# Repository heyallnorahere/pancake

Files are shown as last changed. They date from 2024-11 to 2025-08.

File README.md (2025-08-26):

# pancake

Pancake bot.

CAD drawing can be found [here](https://cad.onshape.com/documents/24af23b84924bcae2e494b27/w/7822e903a0ddc4106c8a2e95/e/12f5b05b2e40a2d157e12141).

Robot
*final robot*

## What is this?

This is a robot based on a "swerve" drivetrain as seen in FIRST Robotics Competition (FRC). The goal
of the project is to build a robot from the ground up, with the only caveat being that off-the-shelf
FRC parts are used exclusively for motors and electrical systems.

A characteristic of the swerve drivetrain is that the robot can move in a linear direction and
rotate at the same time. This is achieved through independent motion of all "modules" - a "module"
controls the motion of one wheel. Each module has the capability to both orient its wheel
independently all of the other wheels and also drive the wheel at the same time. This works with the
use of 2 motors per wheel - one which drives the speed of the wheel, and one which controls the
angle at which the wheel applies force. As a result of this design, my robot is able to move in a
linear direction and rotate concurrently.

Instead of using a roboRIO as robots in FRC do, this project uses a Raspberry Pi. I chose this in
order to build my own tech stack, instead of depending on the robot control systems that are
pre-built for FRC. I also used a single-board computer such as this in order to use low-level APIs
such as CAN without relying on vendor libraries to control motors and such.

This robot is not FRC-legal. The main component which disqualifies it is the custom tech stack which
I wrote on top of ROS and the Raspberry Pi.

## But why?

I started this project to create a deeper understanding of the process of designing and building a
robot. When starting on my local FRC robotics team, I was confined to the bubble of the programming
sub-group. I used this project to break out of that bubble and engage in more aspects of the
process, such as CAD, electrical systems, mechanical assembly, and the interface between user-space
robot code and electrical I/O.

I chose the object of just recreating a swerve drivetrain because it was a complex idea that would
produce a cool result. I had an intuition for how it worked when I was just working on the team, but
I wanted to find out for myself how easily it was implemented and what concessions had to be made
for practicality.

## How?
### Spinning a motor
#### CAN interface

In FRC, CAN is the primary protocol with which the roboRIO interfaces with motors. The Raspberry Pi
does not come with a native CAN interface, in contrast to the roboRIO's built-in CAN ports. With
this being said, however, commercial auxiliary CAN hats can extend the Raspberry Pi's hardware
functionality through the use of the Raspberry Pi's
[SPI](https://en.wikipedia.org/wiki/Serial_Peripheral_Interface) interface, and provide a CAN
network exposed to user-space Linux programs, such as my robot code.

#### SOLO

I chose a Raspberry Pi to control the robot for several reasons. It's cheap, supports a widely-used
operating system, runs on very little power (<1 amp @ 5V), and it does not require an SDK or
specialized development environment to develop for it. While researching the requirements for this
project, however, it was very difficult to find any motor controllers that fell within the budget of
this project while also being guaranteed to work on any CAN-supported computer.

The best candidate I could find that fit both of these criteria was
[SOLO Motor Controllers](https://solomotorcontrollers.com), based out of Europe. Specifically, their
UNO v2 controller with its 45A max current. The only issue was that one controller costed 239 euros
(around 278 USD). Despite the cost, however, this was still the cheapest option that was not
confined to a proprietary ecosystem. I ordered 2 controllers for testing and development purposes so
that I could design and build a module while waiting for more to arrive.

SOLO controllers communicate with their controlling devices via CANopen, among other supported
protocols. I decided to stick with a CAN protocol due to its proliferation in FRC. SOLO provides
a library in both Python and C++ to communicate with their controllers. I was drawn to using their
C++ API due to my familiarity with native programming. However, the C++ library was written locked
to Windows, and my device of choice was running a distribution of Linux. It's not very feasible to
install Windows on a Raspberry Pi, nor was embedding Windows an attractive option from a familiarity
perspective. I had an Intel Nuc that I had installed Windows on, however it was not common to attach
a CAN interface to a computer through USB, and I was also just averse to Windows. I had already
bought a CAN hat for the Raspberry Pi, so the Python API seemed like my best option, as
uncomfortable as I was with the language.

#### NEO Vortex & NEO 550 motors

The most common type motor in FRC is **brushless DC** (BLDC). These motors generally have high
torque and top speed. Initially, I planned to drive both the wheel's speed and orientation using the
same kind of motor, the [NEO Vortex](https://revrobotics.com/rev-21-1652) from REV Robotics. I chose
this motor because it has a relatively high stall torque, and it is widely used in FRC.

This motor is designed to work with either a [SPARK Flex](https://revrobotics.com/rev-11-2159)
controller or a [Solo Adapter](https://revrobotics.com/rev-11-2828) together with a
[SPARK MAX](https://revrobotics.com/rev-11-2158) controller. Due to my previous initial decision of
using a SOLO controller, I decided to buy 2 of both Vortex motors and Solo Adapters. Before I did
this, however, I emailed REV Robotics to verify that a Solo Adapter would work with a generic BLDC
motor controller, to which they affirmed yes. With their confirmation, I ordered the motors and
adapters.

When the Vortex motors and SOLO controllers arrived, I decided to wire one set up for testing.
I assembled the motor onto the Solo Adapter, connected the three phase wires to the SOLO controller,
and powered the SOLO controller with an oscilloscope power supply. However, I also needed to connect
the internal encoder to the controller. The encoder allows the computer to receive feedback from the
motor about how fast it's moving, and how much it's moved since it was powered on. I cut the 6-pin
JST encoder cable that came with the Solo Adapter to half length, and soldered it to the
smaller-pitch 6-pin JST cable, using mappings for the cable found on
[REV's docs](https://docs.revrobotics.com/brushless/spark-max/specs/encoder-port) and the UNO v2
[user manual](https://solomotorcontrollers.com/wp-content/uploads/materials/SOLO_UNO_v2_SLU0722_5832_UserManual.pdf).
This allowed me to spin the motor through the controller's UART interface.

When I began designing the module, I realized that for module azimuth, I did not need
nearly as much torque AND speed as the Vortex provided. In order to minimize both power usage and
project cost, I replaced the azimuth motor with a [NEO 550](https://revrobotics.com/rev-21-1651)
motor in my design, and ordered one motor. I also connected the motor to a set of gearboxes which
decreased its gear ratio by 1:12, increasing its torque while decreasing the speed at which the
wheel rotates in relation to the motor's speed. This can be easily accounted for in code.

#### SPARK MAX

As I was noticing the corner of unfamiliarity I was backing myself into with my developing tech
stack, I decided to send an email to REV Robotics concerning the API for their proprietary motor
controller, the SPARK MAX. I was familiar with this controller due to my experience programming on
an FRC team. This seemed like an amazing alternative to SOLO due to its much cheaper cost of 90 USD.
I asked if there was a library for desktop development environments that I had missed for
communicating with their motor controllers, or if they could provide me with the CAN protocol details
if they did not have such a library published. To my surprise, they sent me a spreadsheet describing
the details of SPARK MAX CAN frames. This gave me a viable alternative to the much more expensive
SOLO controllers.

After careful consideration, I decided to substitute the SOLO controllers for SPARK MAXs. I scrapped
the Python code that I had written to communicate with the controllers, and I ordered 1 SPARK MAX,
learning from my mistake previously of ordering 2 controllers to test. It was also convenient that
the controllers shipped from the US, rather than Italy.

As I now had to write my own API for CAN communication, I was able to write my new stack in a
language I was more familiar with. With Python off the table, I was opting towards C++. I briefly
considered Java, being both the most common language in FRC and also the language that my team works
in. However, I would need to waste time working with the Java Native Interface, communicating
directly with the Linux kernel. This seemed like too much of a hassle in a language that was both
abstracted from low-level APIs and not my language of choice, so I decided to stick with my comfort
language: C++.

CAN on Linux works by opening a socket on the `canX` network, with `X` being the interface index.
This allows one to send CAN frames on the electrical CAN network via the ubiquitous Linux socket
API. Through Googling I came across this great
[document](https://kernel.org/doc/Documentation/networking/can.txt) which describes how the socket
CAN interface is used. This greatly sped up the software development process.

There are many protocols through which functionality is exposed over CAN. The most common one by far
is CANopen, which is used in industry robotics and medical equipment. FRC, however, has
[their own CAN protocol](https://docs.wpilib.org/en/stable/docs/software/can-devices/can-addressing.html).
Even so, this specification does not explain on its own how to communicate with one specific kind of
motor controller. This in combination with the spreadsheet that REV support shared with me made it
possible for me to begin working on my own library to communicate with SPARK MAX controllers.

After much writing, debugging, and emailing, I was able to write my own vendor library to control
DC/BLDC motors through SPARK MAX controllers. However, REV stipulated that I cannot share the
details of the CAN spec, so the `vendor/librevfree` submodule (the library that I wrote to interface
with the motor controllers) is not made public.

I had issues with motor controllers later down the road. Accordingly, I continued to commit to the
library as I was developing the robot. It's very hard to write your own library and use it without
finding issues.

### Software development

FRC relies upon a proprietary control system integrated with an NI roboRIO. It sends signals through
the control client to dictate which WPILib routines run on the roboRIO ("Teleop" or "Autonomous")
during various phases of each FRC match. It also handles controller input during the teleoperated
mode to allow the user to control the robot directly.

As I was operating in my own development environment, I had none of these luxuries. I had to choose
how exactly I wanted to design my robot system.

#### Communication via ROS & Docker

Because this project uses a Raspberry Pi, I needed some way to communicate with a control system. I
used ROS (**R**obot **O**perating **S**ystem) to achieve this. ROS is a tech stack designed for
interoperation between multiple processes running either on the same computer or multiple in a
closed system. It natively supports C, C++, and Python, which fit any conceivable use case I had for
it in this project. 

An ROS application consists of a system of "nodes," individual processes on various devices which
send arbitrary messages to each other. The ROS message system is identical to FRC's
publisher/subscriber system, where server nodes send messages on "paths" akin to Unix file paths for
client nodes to listen to.

ROS is not natively supported on any Linux distributions other than Ubuntu. The Raspberry Pi only
directly supports its own version of Debian called Raspberry Pi OS, or Raspbian. Although Ubuntu is
closely related to Debian through its package manager and source tree, the two distributions use
different package repositories, and for the robot's runtime environment, I wanted the package
manager system to be as clean as possible, without any hacked-together package manager
configuration.

I considered installing Ubuntu on the Raspberry Pi that I mounted onto the robot, however Docker
seemed like a much better choice. Docker is a background process that runs containerized versions of
operating systems pre-installed with a desired program. It's useful for "shipping" the *exact*
runtime environment that you want your program to run in. With Docker, I could control explicitly
for the runtime environment of my project using my custom-built Docker image.

Docker also allows the image to have controlled access to the host computer's peripheral devices.
This includes the CAN network and game controllers. Passing through the host networks and input
devices, I was able to precisely control the methods in which my program could interact with its
host environment. This is very useful for creating security sandboxes, minimizing the chance that a
vulnerability in my tech stack could compromise my workflow and the end product.

Deciding to ship my software stack with Docker, I set up a Docker build in my code tree. As I was
hosting my project's code using a private Github repository, I had limited monthly access to Github
Actions, their CI/CD system, a service which runs automated tasks when it receives events. My access
was limited by job run time, however my builds were infrequent enough that I was able to build the
Docker image for both x86 and ARM architectures every time that I pushed a commit. As I used CI/CD
more frequently, and I wanted to control the hardware that it was built on, I began using a desktop
computer installed with an Ubuntu server to act as an Actions runner for my project, lifting the
usage restrictions.

#### Cross-compilation

Single-board computers such as the Raspberry Pi run on the ARM CPU architecture. This differs from
the x86 architecture that most desktop, laptop, and data center machines run on. However, because I
was developing the project in C++, and the native Linux ELF binaries that C and C++ compile to
cannot run on architectures they were not compiled for, so I was forced to compile my ROS project
explicitly for `arm64`. Initially, I emulated the `arm64` architecture during the Docker build via
QEMU in my CI/CD workflow. However, each build took around 30 minutes due to the compiler overhead
introduced with C++ templating, and the proliferation of templates in the ROS C++ client library.

The more efficient approach I devised was to segment the Docker build into two stages: `build` and
`runtime`. The `build` stage runs on the native architecture of the compilation machine, while the
`runtime` stage runs on the target architecture that the image will be built for. The project is
cross compiled in the `build` stage using compiler wizardry and
[shell scripts](scripts/buildenv.sh). After this, the binaries are copied into the `runtime` stage,
and the robot code can run natively on the Raspberry Pi through the Docker hypervisor.

#### Robot input & SDL

FRC uses conventional game controllers to control competition robots. The most common controllers
used are those of the Xbox 360, Xbox One, and PS4. These controllers are all supported by
[SDL](https://github.com/libsdl-org/SDL), a library for GUI applications with real-time input,
designed for applications such as game development. As I was already familiar with the library's
usage, I decided to use this library to handle controller input on the robot. It can be built
headless (without windowing support) using a configuration flag (`-DSDL_VIDEO=OFF`) so that it
builds in less time without unnecessary features.

I used SDL in an independent `client` ROS node to handle controller input from the user, and pass
messages along to the `robot` node. I also wrote a simple GUI client in the same `client` node using
[Dear ImGui](https://github.com/ocornut/imgui) in case the library was built with video support,
i.e. in desktop environments for simulation and remote control.

#### Drivetrain control

The main meat and potatoes of my application is in the `swerve` ROS node. Receiving messages from
its controlling `robot` node, it derives motor voltages from the `robot` node's "request" using
geometric, trigonometric, and physical principles. It then sends CAN messages to the SPARK MAX motor
controllers, which use their respective motor to produce torque on that motor's axis.

After it sends signals to its motors, it then uses the feedback of velocities reported by
aforementioned motors' encoders to determine the current velocity of each module. The data collected
on each module is then used to determine the linear and angular velocity of the entire robot in
order to inform how it continues to control each module. All of this data is published back to the
ROS message system for the `robot` and `client` nodes to use.

#### Self-updating & bluetooth controller pairing

I wanted this project to have the capability to run without any external computers or monitors. For
this purpose, I wanted to expose two helpful functions on the actual chassis of the robot:
self-updating and controller connection.

Due to the containerized nature of this project through Docker, new versions are easily installed by
downloading a new image and recreating the container using the newly-downloaded image. Because of
the simplicity of this process, a project called
[Watchtower](https://github.com/containrrr/watchtower) exists to automate it. With an option, it
exposes an HTTP REST API which allows clients to send HTTP requests to trigger container updates.

I wrote another containerized [program](https://github.com/heyallnorahere/robot-util) to expose this
functionality through a text UI on a small $10 20x4 HD44780 I2C LCD screen. It handles automated
image updates through a menu option which is selectable through a rotary encoder connected to the
Raspberry Pi's GPIO pins. I wrote this program in C both to stretch myself with a minimalist
programming language and because the program itself was not inherently object-oriented as the swerve
drivetrain was. It's containerized with Docker similarly to the actual robot code, and self-updates
through the same mechanism through which it updates the robot code.

I also created menu functionality to pair bluetooth devices. This is useful for pairing console
controllers, as oftentimes these controllers connect to their respective console through bluetooth.
This allows one to pair a controller to control the robot through the LCD screen, instead of having
to `ssh` into the Raspberry Pi and pair it manually through `bluetoothctl`.

### Chassis design

As the goal of this project was to gain experience with all aspects of robot design, I designed the
entire robot chassis from the ground up. In FRC, it is standard practice to buy manufactured swerve
modules from hardware vendors (i.e. REV, Swerve Drive Specialties), as the drivetrain is not the
primary hurdle of robot development. However, my focus was primarily on the intricate design process
of the *entire* robot, including the swerve modules. These were the first steps in robot
development.

#### CAD

Before this project, I had acquired some CAD (**c**omputer-**a**ided **d**esign) experience. In the
past, I had designed some robotics-adjacent projects with CAD software, however these projects never
came to fruition. This project seemed like a perfect opportunity to brush up on my CAD skills.

The software suite that I chose for this project was Onshape. Onshape is very commonly used in FRC
design teams, and I had used it in the past with physically-designed projects. It's also very
feature-complete with an extensible API for creating additional features.

#### Materials

The vast majority of mechanical parts in FRC are manufactured out of aluminum. During development, I
did not have access to a CNC router, so I chose the next best option, which I had plenty of
experience with: 3D printing. 3D printers can manufacture parts with plastics of varying tensile
strengths, which gave me confidence in the approach.

For parts such as gears that experience large amounts of force over very little surface area, I
decided to print with ASA (**a**crylonitrile **s**tyrene **a**crylate) filament, a thermoplastic
commonly used in the manufacturing of mechanical parts. However, as I was prototyping with PLA
(**p**oly**l**actic **a**cid) infused with ABS (**a**crylonitrile **b**utadiene **s**tyrene), I
found that parts printed completely filled with plastic held up very well under simulation of the
stress that they would experience. Drawing from this discovery, I decided to manufacture all parts
used in the swerve modules and electronics mountings with this blend of PLA and ABS.

I assembled the modules to the rest of the components using custom-cut 20x20 aluminum extrusions.
These were preferable to long, segmented 3D printed parts because the alternative would not be
nearly as structurally stable, nor would it be time- or cost-effective in comparison to extrusions.

#### Structure

Due to the flexibility in which one can design parts for 3D printers, and the availability of
breakaway support material, designing the structure itself was trivial. Each module consists of two
main plates, supported between each other with 3cm-long printed standoffs. 3D-printed parts are
extremely strong under compression, which led me to use them as nothing more than spacers, held in
place by M3x50 bolts on the top and M3 nuts on the bottom.

As the large majority of the module's weight lies on the top plate, it's very important that it's
adequately supported. With some quick Googling, I determined that PLA plates should be supported
roughly every 5cm. I shortened this slightly to 4.2cm both for convenience in my design and to
create a margin for printing and assembly error.

#### Hardware

Wherever possible, I stuck with metric units and bolt sizes. I had quite a lot of M3 hardware lying
around, so I used M3 whenever I could. However, I had to make some exceptions. To secure the two
internal drive gears to their respective shafts, I used an M2 bolt threaded through a nut in a small
pocket on the internal circumference of the gear. M3 screws were too large. In my mount for the
Raspberry Pi, I had to use M2.5 bolts to fit through the RPi's mounting holes. Additionally, all
FRC-legal parts use #10-32 bolts. In addition to the irritation of using imperial units, I did not
have any #10-32 hardware in stock.

I mounted each individual part onto the aluminum extrusions which joined the chassis together with
drop-in M3 T-nuts. On the uncut extrusions which I already had in stock, the T-nuts dropped in
perfectly. However, when the custom-cut extrusions I ordered from Misumi arrived, the lips on the
new extrusions did not allow the T-nut to drop in. This created a slight inconvenience whenever I
added a new part to the chassis, as I had to remove the entire extrusion from the chassis and slide
the necessary quantity of T-nuts down the shaft.

#### Design details

For a reference of how swerve modules commonly work, I at the CAD drawing for
[REV's MAXSwerve module](https://revrobotics.com/rev-21-3005/). As a result, the module was loosely
based off of this design. I also used their wheels in my design.

The module uses two motors in coordination to orient and drive the wheel independently. The module
is also fitted with a duty cycle encoder to measure the distance from the module's "default"
position. This allows the motors to control the direction and magnitude of force which the module
is exerting on the robot's chassis while also sending feedback to the robot's controlling device.

The drive motor has a nearly inconsequential gear ratio because the motor produces a large amount of
torque on its own. However, I attached two gearboxes to the rotational motor to decrease its gear
ratio by 1:12. This is further decreased by its 1:4 relation to the output orientation of the wheel,
which leaves the axis with a gear ratio of 1:48 to maximize torque.

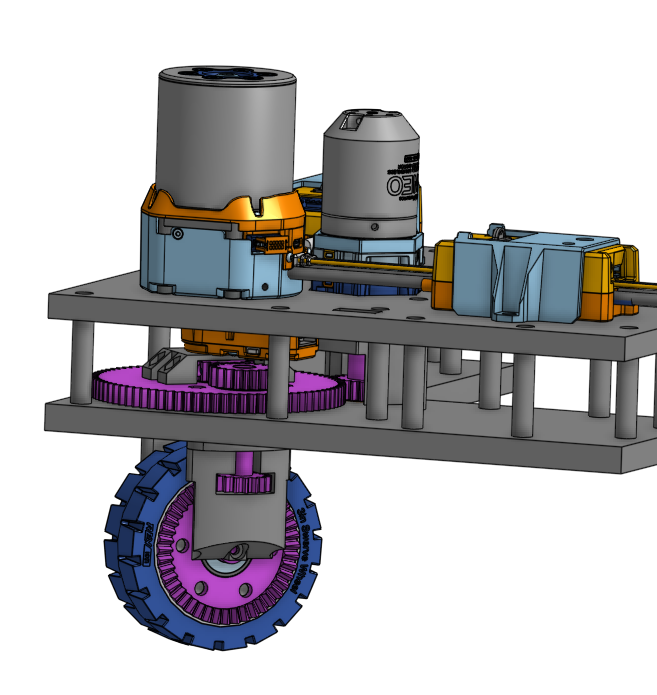
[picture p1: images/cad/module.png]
Module CAD

*CAD drawing of swerve module*

### Electronics

Robots need power. A lot of power.

#### Power delivery

FRC robots run on a nominal voltage of 12 volts. Typical SLA (**s**ealed **l**ead **a**cid)
batteries as used in FRC generally produce a voltage slightly higher, at 13 volts. To mimic the
final environment of an SLA battery, I ran motors on a 13V wall power supply while prototyping.
However, when I attached the modules to a full chassis, I began running the robot off of battery
power.

The battery is fed into a 120A breaker, common in FRC robots. This creates a hard upper limit for
the robot's power draw, mitigating the damage of short circuits and stalled motors. It also provides
a switch to turn the robot on and off immediately, a safer mechanism than simply attaching the
battery.

All power in the robot runs through a centralized device called a PDH (**P**ower **D**istribution
**H**ub), another FRC-standard component from the vendor of the motors and controllers I was using,
REV Robotics. It distributes power to multiple channels, each limited with a fuse or breaker. The
PDH was also ideal for testing and iteration, with WAGO clips on each channel for both VCC and
ground, as opposed to permanent crimping or soldering. The battery cables from the breaker run
directly into the PDH, where it distributes power and limits current draw from each motor.

I used 12AWG wire to connect the motor controllers to the PDH. 12AWG wire is rated for 20A
continuously, with a fusing current of over 200A. This was ideal for my application, as the maximum
current between both kinds of motor was 45A, and the force required to move the robot was not
particularly high. These wires were connected to the motor controllers with WAGO connectors,
similar to the PDH terminals.

#### Cable management

Due to the mobile nature of this project, I needed to organize cables very neatly to avoid snagging
on any variation in the surface on which it's driving. Wires snagging on external objects could
cause power loss and short circuits, which at 12 volts could potentially cause significant damage to
the robot and its environment.

To simply cable management, I used paired red and black 12AWG cable to deliver power to the motor
controllers. I also ran cables along the 20x20 extrusions of the chassis' frame to avoid a rat's
nest in the empty portions of the frame.

I initially considered zipties to fasten cables to the extrusions. However, these are very wasteful,
with any electrical change creating plastic waste in the form of the previous tie. Because of this,
I chose to use velcro cable ties, reusable organizational ties which fulfill the same purpose as
zipties.

## Overarching challenges

**Lack of documentation**. I initially chose SOLO controllers because SPARK MAX controllers,
although clearly the better alternative, did not have publicly available CAN documentation. Even
after emailing REV, and working with a spreadsheet of CAN IDs, I still struggled to piece together a
viable control library. I had to decompile the native roboRIO REV library with
[Ghidra](https://github.com/NationalSecurityAgency/ghidra) to find memory layouts for status frames
undocumented in REV's spreadsheet. Additionally, as the new FRC season started in January 2025, REV
released a new version of firmware which dramatically changed the CAN API. After struggling to find
any data related to this new firmware version, either through REV support or in decompiled C++ code,
I opted to use an older version of the controller firmware.

**Iteration times**. C++ code that includes ROS headers took significantly longer to build and
therefore iterate upon due to the prominent use of templating within the library. I mitigated build
times by optimizing the build process (i.e. building image on native architecture, minimizing header
inclusion in code), however each build of my robot code took around 10 minutes. Additionally, when
designing the robot in CAD, I made several mistakes in designing each part. Most parts in each
module on either the module's top or bottom plates, and so a part change often meant I had to
re-print one or both of the plates. Each plate took slightly less an hour to print, so at the worst,
one print to fix one part took upwards of 2 hours. This combined with reassembly time
dramatically slowed the build process.

**Module mounting**. The module was just slightly too thick between the top surface of the top
plate and the bottom surface of the bottom to mount onto aluminum extrusions on the bottom of the
module with M3x50 bolts. M3x60 bolts were slightly too long to create a strong connection between
the module and the robot frame, and M3x50 bolts had to be forced into the T-nuts on the bottom. To
solve this issue, I ordered non-standard M3x55 bolts, which cost significantly more than M3x50s or
M3x60s and took nearly a week to arrive after I realized the issue, however they were able to create
a strong mechanical connection when suspended above the bolt's counterbore slot with a washer.

**UltraPlanetary bolt snugness**. The azimuth motor's output is fed through two REV UltraPlanetary
gearboxes which decrease its gear ratio by 1:12. These gearboxes are fastened to the module and
motor using 6 M3x30 bolts fed straight through the gearboxes into the motor. The issue with this
design arises when the bolts are fastened too tightly, and the friction of the system increases
dramatically. However, when the bolts are not fastened tightly enough, the motor begins shifting as
torque is applied, damaging the motor over time. Additionally, the bolts loosen very easily. I
solved this issue by using locktite to lock the bolts in place relative to the motor, gearboxes,
and module.

**Module inversion**. As I was preparing to test the robot moving on the ground, I noticed that two
modules were spinning inverted from the direction they should have been spinning in. This bug took
me 4 days to fix, and was caused by three main things. I had confused the spaces in which the wheel
well was rotating. I had also normalized an angle incorrectly, leading to incorrect angle values
when performing math to determine in what direction each module should be spinning. Fixing these two
issues fixed one module's rotation, however one was still spinning in the wrong direction. This was
ultimately caused by the duty cycle encoder being calibrated in the opposite direction, which was a
simple human error. Fixing this final issue removed this roadblock.

**Ubuntu package versions and ROS cross-compilation environment**.
[ROS does not support native cross-compilation on the latest distribution.](https://github.com/ros-tooling/cross_compile)
Setting up a cross-compilation environment manually is black-magicky, installing multiple
architectures of the same development package onto the same "machine" (or in this case, image build
container). The Python development libraries a prime example of this, breaking each other when
package versions differ. Unfortunately, the ROS image has this installed by default for the build
architecture, and attempting to uninstall it in the container will uninstall the rest of ROS.
Additionally, the Python package in the x86 repository generally gets a version bump a day or two
before the `arm64` port repository. This makes cross-compilation impossible for the amount of time
the two versions differ, because the `arm64` version is not installable without the entire
uninstallation of ROS. Thankfully, this was only an issue once in the development process.

## What went well?

**Final product fit within original project parameters**. The overall design of the robot did not
differ from my original vision when starting the robot. Originally, I was going to use SOLO
controllers, but I switched to SPARK MAX controllers before mechanically designing the robot in CAD,
so no major reworks needed to be done.

**FRC skills**. As one of the main stated goals when starting this project, I made sure to design
the robot as similarly to an FRC bot as I could. This led me to design the robot from the ground-up
as somebody on the design team would; I connected and organized CAN, power, and encoder wires as one
on the "systems" team would do; and I assembled the robot from the ground up, gaining me experience
with the "mech" team process. I also had the opportunity to delve into the FRC-flavored CAN
protocol, which is a step up from my previous experience on the programming team.

**No major electrical mistakes**. Even though it takes a large voltage to send a dangerous current
through the human heart due to the resistance from the end of one arm to the other, short circuits
directly between battery leads are potentially very dangerous. For this reason, I kept all wires
under fuses when possible, and I kept the PDH unplugged from power while managing wires. Because of
this, I never had any major electrical incidents while working on the robot. The only mistake that I
made in this regard was a particularly unfortunate accident when I sent a static shock through the
CAN hat of the Raspberry Pi and fried the board with a short. The Raspberry Pi was not harmed at
all, however I had to replace the CAN hat which cost $60 and a week.

**Communication protocol**. ROS supplies a robust real-time communication framework for coordination
between ROS nodes. This allowed me to easily segment the codebase and handle user input
independently of drivetrain math and motor control, among other development niceties.

**Automated build process**. As a result of my cloud-based cross-compilation setup, I was able to
streamline my workflow to automatically build and deploy my code every time I push a Git commit.
This allowed me to push my code to the robot and check in my current code state in one command in
Neovim, my code editor of choice.

**Self-contained final robot**. Early on in the project, I made the decision to consolidate all
necessary functions into the robot itself. This includes connection and collection of user input,
and also code updates. I implemented the self-contained connection of controllers using the Linux
BlueZ bluetooth stack, and I passed all user input devices through to the Docker container driving
the robot to be handled by the headless `client` node. I also implemented self-updates using
`watchtower` in combination with my LCD text UI, thus allowing the user to completely control the
robot and its software without the use of a shell.

## Lessons learned
### TRIPLE CHECK

This goes for CAD, programming, electrical work, all of it. Triple check your work! Do not write or
do something once and call it good. In CAD, make sure that one change in a seemingly unrelated area
did not break a part somewhere else. In software, unit test areas of code individually and
iteratively before testing it on the robot. In electrical work, triple check that all wires are
connected to the right components. All of this will solve so many debugging headaches.

### DONT BE LAZY AND FIX PROBLEMS

I spent too much time twiddling my thumbs while waiting for my robot code to build in Github CI.

XKCD 303 (https://xkcd.com/303/)
*XKCD 303: Compiling*

Before I sped up the build process by 1. hosting the build on my own server and 2. cross-compiling
code rather than emulating the compiler with QEMU, I thought, "it can't be helped. I need to just
keep working while the build finishes." This ultimately exaggerated iteration times and slowed the
build process.

Finally, I invested time into fixing the build system. With the ~5 hours that it took to get this up
and running, I had more than made up for the >15 (5 * 60 / (30 - 10)) builds that I had triggered by
that point. With a 10 minute build time, I was able to iterate at a much faster pace, allowing me to
dramatically speed up the development process.

### FINALIZE CORE COMPONENTS BEFORE ORDERING

I wasted around slightly less than $600 on SOLO motor controllers. The only reason I found it
reasonable to spend this much on motor controllers is that they are one of the core components that
makes this project possible. What I should have done before ordering the SOLO controllers was
confirm, beyond a shadow of a doubt, that these controllers were the ones that I would use. Although
it was ultimately beneficial that I emailed REV, I should have done that in the first place before
deciding on a motor controller.

### NEW TECHNOLOGIES USED

In the process of creating the end product, I introduced myself to quite a few new technologies. To
name a few, I familiarized myself with CAN for motor communication, the Linux D-Bus for
communication with the `bluetoothd` daemon, and cross-architecture C and C++ compilers and build
tools for my cross-compilation Docker toolchain. I also gained a lot of practical experience with
CAD, which greatly helps any personal and team projects that I might participate in. It is almost
always beneficial to use new and unfamiliar technologies in non-commercial projects in an effort to
become more well-rounded as a software developer.

### STAY ON TASK

I spent a few days trying to read data from the PDH over CAN for motor power usage metrics. This did
not end up proving useful or necessary, nor was it part of the project parameters, and I ultimately
just wasted my time. I could have used this time to work further towards the material goal of
finishing the robot.

### SAFETY FIRST AND BEFORE EVERYTHING

The incident with frying the CAN hat easily could have been avoided if I followed electrical safety
procedures. This happened in May, and it was particularly dry around this time. As a result, I
easily accumulated static charge by performing basic tasks. In addition to this, I was wearing a
cashmere hoodie, and my long hair was not tied back. When I went to rearrange CAN wires, I did not
ground myself before doing so. I accidentally delivered a static shock which stuck the board in a
configuration state.

I could have avoided this if I took my hoodie off, tied my hair back, and grounded myself before
working with delicate electrical equipment such as this. Safety procedures exist for a reason.

### DEBUGGING IS BETTER THAN NOTHING

While I was debugging the issue of inverted wheel rotation, I was confident that the issue was
ultimately in my swerve math. While this was somewhat correct, I was stuck looking over my math code
for around a day. Finally, I swallowed my pride and brought up a Docker container with `gdb` set up.
I had initially avoided this because I had only debugged code in an IDE's UI before. Additionally,
because the Docker build was segmented and the runtime stage did not have the source included in the
container tree, I had to cross-reference debugger output with my current source tree in Neovim.
Nonetheless, using a debugger greatly sped up my debugging process, and it likely allowed me to
solve the issue much quicker than if I had not brought up a debugger. I learned that I need to
broaden my approach to solving problems, consider new approaches that I had not tried yet, and check
null hypotheses.

## What's next?

The main feature I would like to implement is autonomous motion on pre-programmed paths, based on
computer vision. I have experience with this in FRC, using libraries such as
[PhotonVision](https://github.com/PhotonVision/photonvision) for computer vision, and
[PathPlanner](https://github.com/mjansen4857/pathplanner) for path generation. These libraries are
built specifically for FRC, so plug-and-play use in my project is likely unfeasible. Implementing
motion along paths seems to be easily achievable with my experience with the library. Additionally,
the University of Michigan provides a native, open-source
[library for detecting April Tags](https://github.com/AprilRobotics/apriltag), the specification of
fiducial tags used in FRC. With both of these components, this feature seems completely feasible.

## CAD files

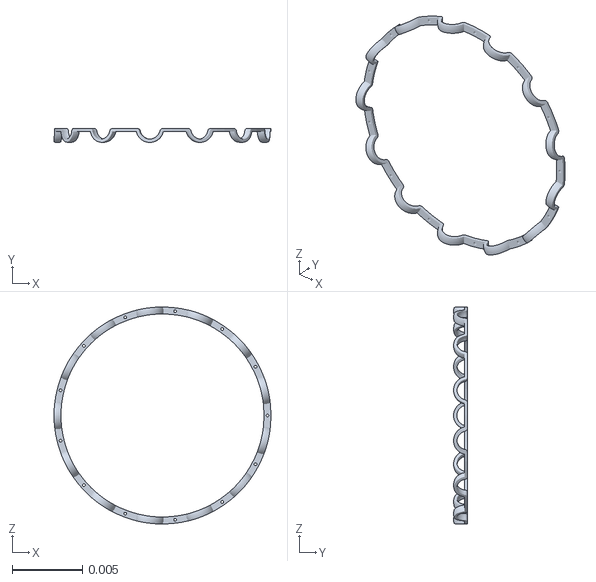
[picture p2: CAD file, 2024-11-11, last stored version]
resource/cage.stl
0.0155 x 0.000994 x 0.0155

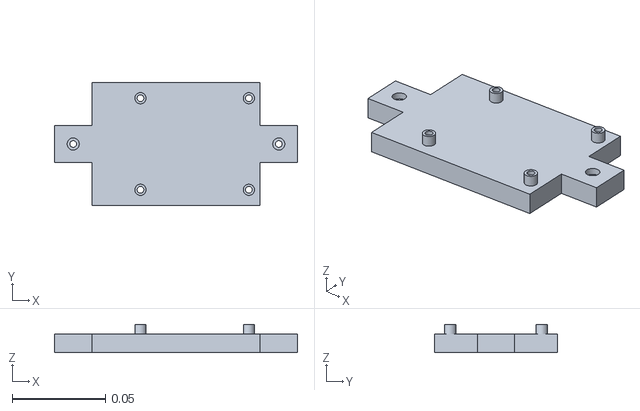
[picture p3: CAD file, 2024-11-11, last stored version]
resource/rpi_plate.stl
0.13 x 0.066 x 0.015

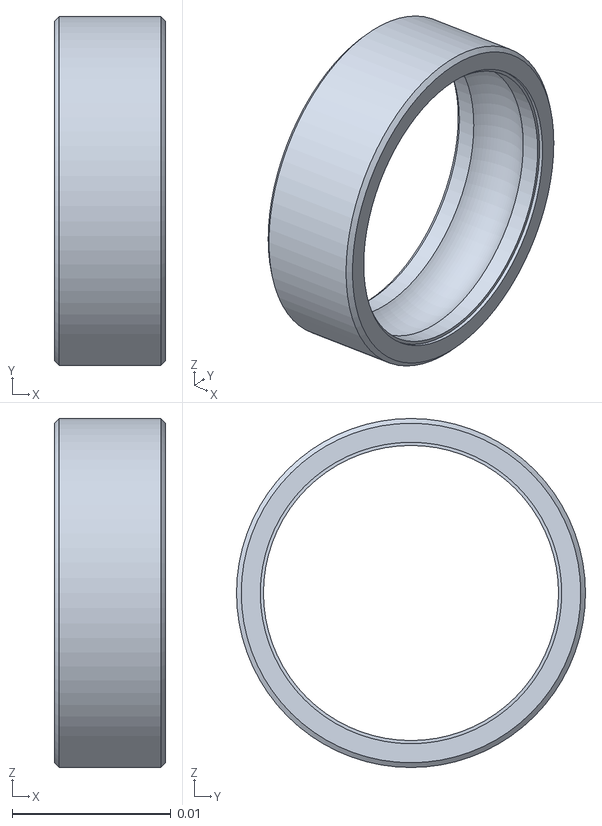
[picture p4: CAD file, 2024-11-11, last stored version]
resource/yttre_ringen_v5.stl
0.007 x 0.022 x 0.022

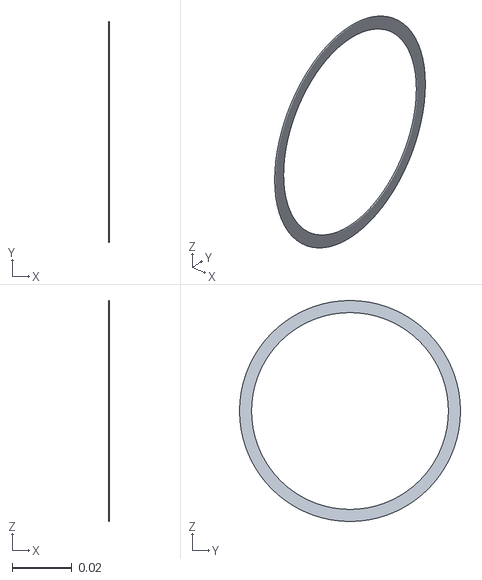
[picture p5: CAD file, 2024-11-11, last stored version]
resource/6812zzst.stl
0.00034 x 0.0738 x 0.0738

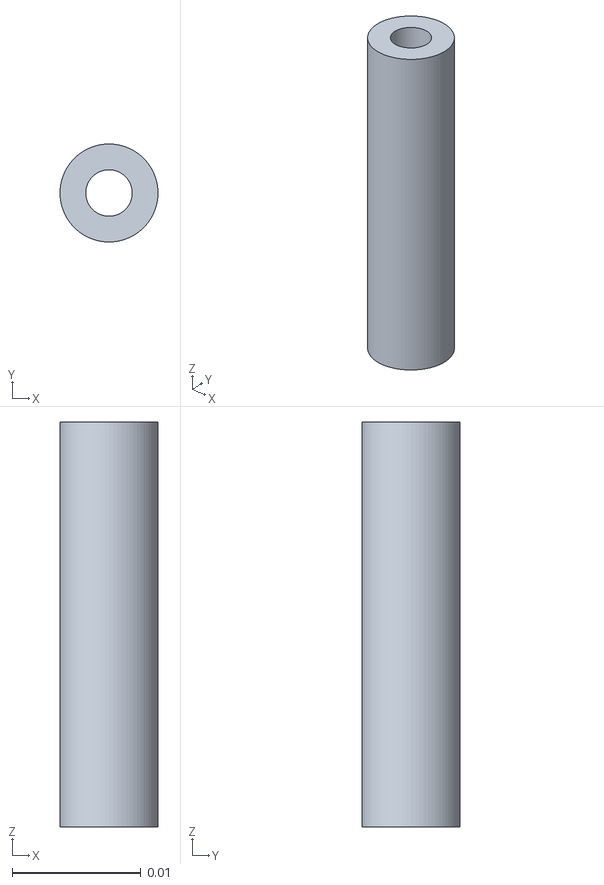
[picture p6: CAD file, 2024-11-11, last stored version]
resource/standoff.stl
0.0076 x 0.0076 x 0.0314

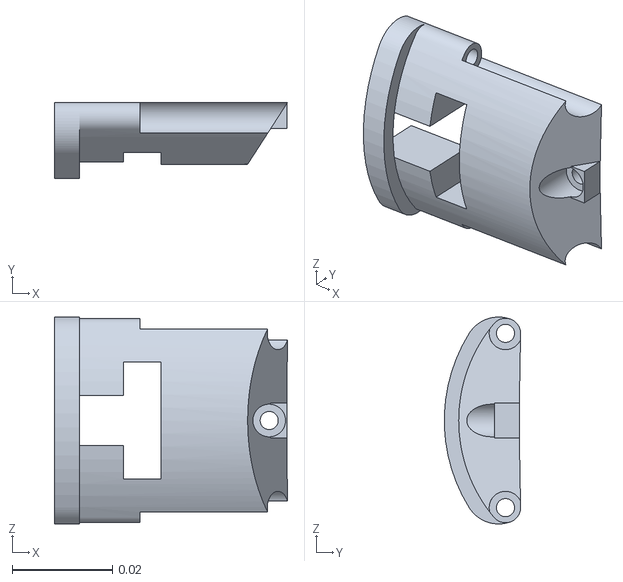
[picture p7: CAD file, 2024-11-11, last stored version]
resource/gear_bracket.stl
0.0464 x 0.0152 x 0.0412

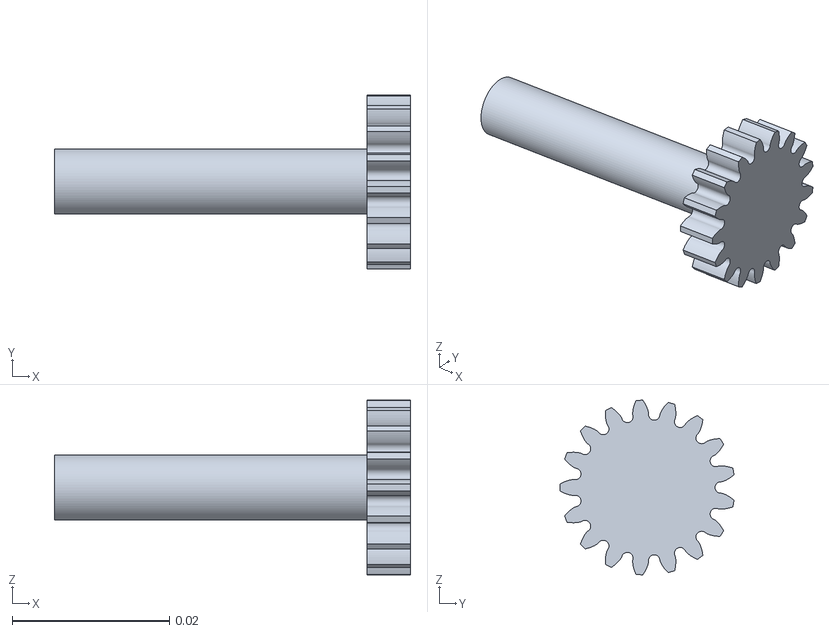
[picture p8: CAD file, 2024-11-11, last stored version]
resource/wheel_well_axle.stl
0.0452 x 0.0221 x 0.0222

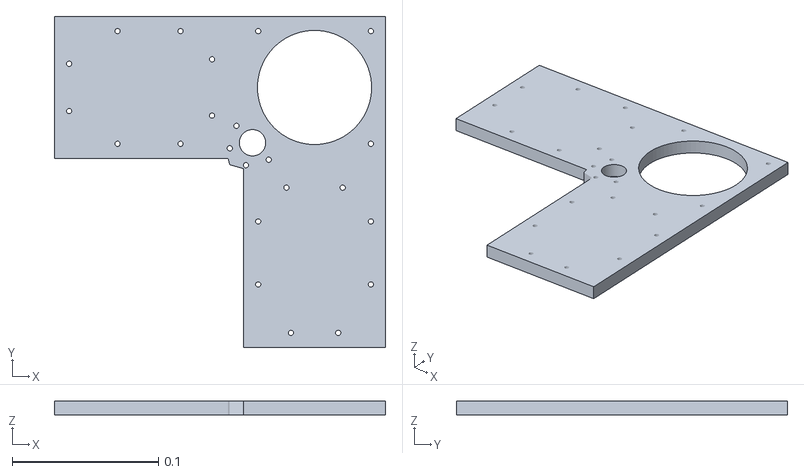
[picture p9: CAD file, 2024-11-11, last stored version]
resource/bottom_plate.stl
0.226 x 0.226 x 0.00988

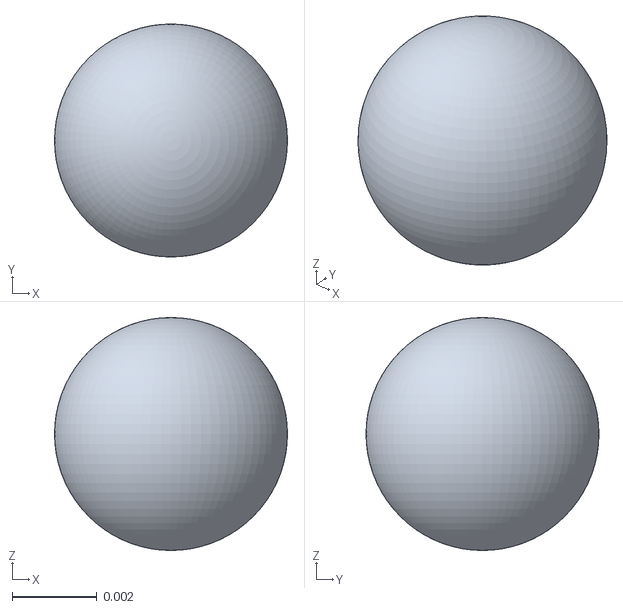
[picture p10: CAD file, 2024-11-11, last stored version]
resource/kula_v2.stl
0.0055 x 0.0055 x 0.0055

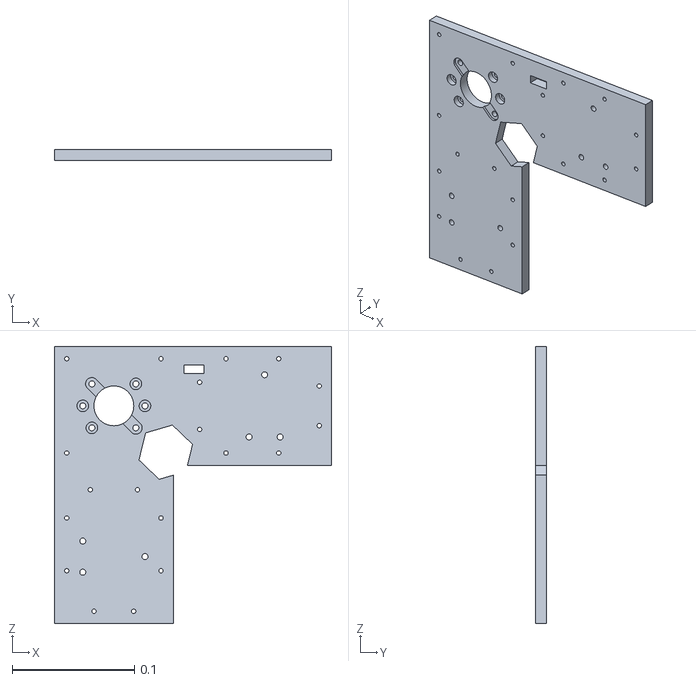
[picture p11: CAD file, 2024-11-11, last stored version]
resource/top_plate.stl
0.226 x 0.009 x 0.226

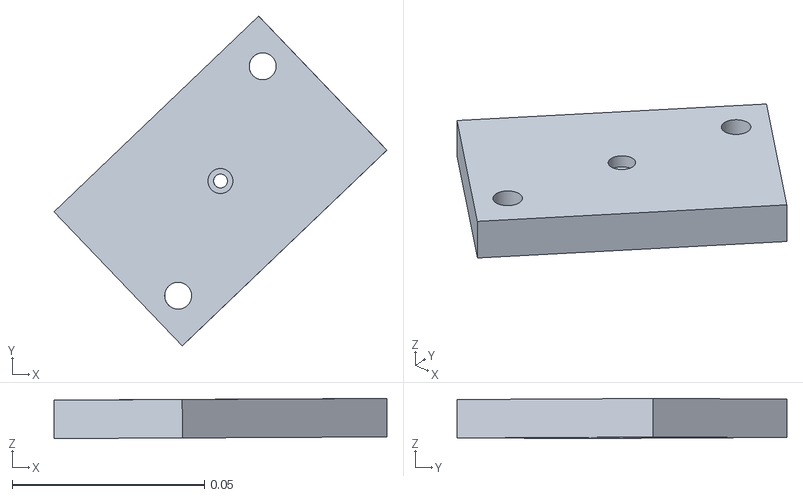
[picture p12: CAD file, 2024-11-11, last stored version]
resource/breaker_plate.stl
0.0866 x 0.0858 x 0.0104

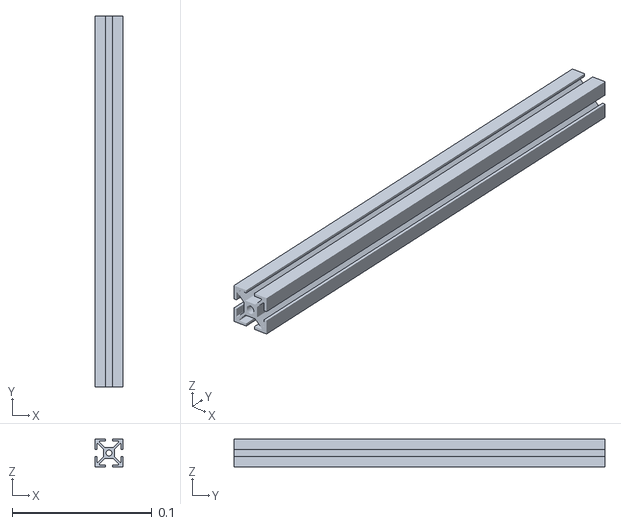
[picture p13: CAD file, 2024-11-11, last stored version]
resource/edge-to-center_crossbar.stl
0.02 x 0.266 x 0.02

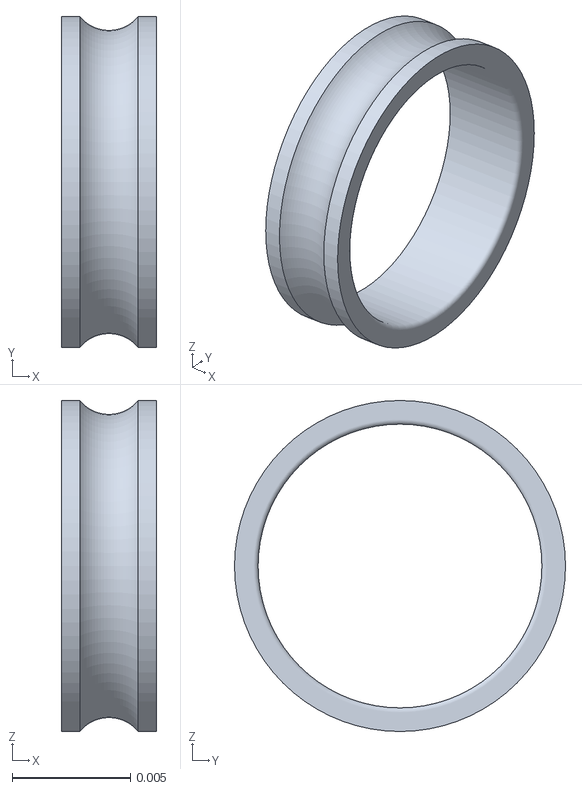
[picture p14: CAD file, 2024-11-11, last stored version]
resource/inner_ring.stl
0.004 x 0.014 x 0.014

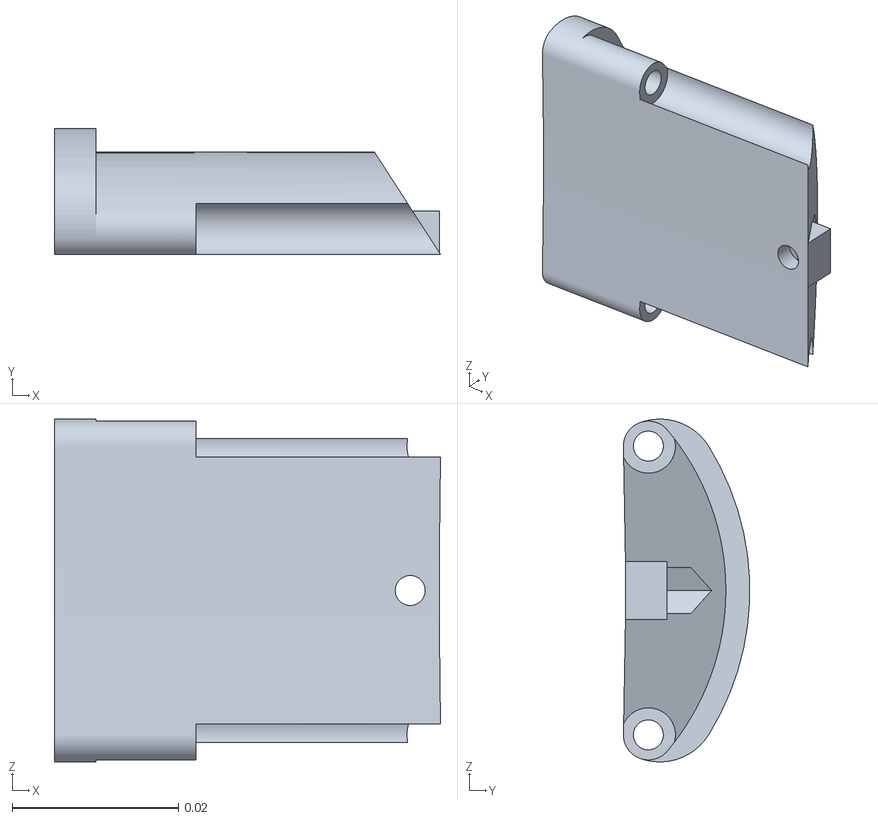
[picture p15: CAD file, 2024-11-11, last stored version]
resource/non-gear_bracket.stl
0.0464 x 0.0152 x 0.0412

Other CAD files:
resource/front_plate.stl
resource/drive_shaft_gear.stl
resource/outer_ring.stl
resource/sla_battery.stl
resource/2020_-_m3_t-nut_v2.stl
resource/6812zz_ball.stl
resource/6812zz_inner_ring.stl
resource/6812zz_outer_ring.stl
resource/aluminium_extrusion_20x20x1000.stl
resource/back_plate.stl
resource/ball.stl
resource/battery_bracket.stl
resource/center_plate.stl
resource/edge-to-crossbar_bracket.stl
resource/mellan_ringen_v3.stl
resource/nedre_ringen_v5.stl
resource/pdh_plate.stl
resource/rotation_axle.stl
resource/rotation_axle_housing.stl
resource/rotation_encoder_bracket.stl
resource/sidoskydd_v5.stl
resource/wheel_axle.stl
resource/wheel_well_gear.stl

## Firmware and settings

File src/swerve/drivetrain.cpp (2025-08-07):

#include "pancakepch.h"
#include "pancake/swerve/drivetrain.h"

namespace pancake::swerve {
    Drivetrain::Drivetrain(const Config& config, bool sim) : m_Config(config), m_Sim(sim) {
        for (const auto& desc : m_Config.Modules) {
            AddModule(desc);
        }
    }

    Drivetrain::~Drivetrain() {
        // we want motors to be dealt with before sim handlers
        m_Modules.clear();
        m_SimHandlers.clear();
    }

    static void DumpRequest(const pancake::msg::SwerveRequest& request) {
        Vector2 linear;
        linear.X = request.velocity.x;
        linear.Y = request.velocity.y;

        static const float rad2Deg = 180.f / std::numbers::pi_v<float>;
        float linearVelocity = linear.Length();
        float linearVelocityAngle = std::atan2(linear.Y, linear.X) * rad2Deg;
        float angularVelocity = request.velocity.angular_velocity * rad2Deg;

        auto logger = rclcpp::get_logger("swerve");
        RCLCPP_DEBUG(logger, "Setting request:");
        RCLCPP_DEBUG(logger, "\tRequest type: %s", request.absolute ? "absolute" : "relative");

        RCLCPP_DEBUG(logger, "\tX velocity: %f m/s", linear.X);
        RCLCPP_DEBUG(logger, "\tY velocity: %f m/s", linear.Y);
        RCLCPP_DEBUG(logger, "\tLinear velocity: %f m/s", linearVelocity);
        RCLCPP_DEBUG(logger, "\tLinear velocity angle: %f degrees", linearVelocityAngle);
        RCLCPP_DEBUG(logger, "\tAngular velocity: %f degrees/s", angularVelocity);
    }

    void Drivetrain::SetRequest(const pancake::msg::SwerveRequest& request) {
        // copy down request
        m_Request = request;

        // make sure we keep logs
        // DumpRequest(request);
    }

    void Drivetrain::ResetOdometry(const std::optional<pancake::msg::OdometryState>& state) {
        auto logger = rclcpp::get_logger("swerve");
        RCLCPP_INFO(logger, "Odometry reset");

        // reset odometry
        // this mainly just resets the heading of the robot
        m_Odometry = state.value_or(pancake::msg::OdometryState());
    }

    Vector2 Drivetrain::CalculateLinearVelocity(const SwerveModuleMeta& meta) const {
        // offset from the robot's heading to the forward vector on the module
        float robotSpaceRotation = meta.RotationalOffset;

        // if the speed request is absolute, then the left stick is talking in terms of the
        // field, not the robot heading, so we offset the rotation offset by the offset from
        // "forward" on the field to the robot's heading
        if (m_Request.absolute) {
            robotSpaceRotation += m_Odometry.transform.rotation;
        }

        // vector from the input swerve request
        Vector2 desiredLinear;
        desiredLinear.X = m_Request.velocity.x;
        desiredLinear.Y = m_Request.velocity.y;

        // convert the requested linear velocity to module space
        // rotate the vector so that +x is on the module's x axis
        return desiredLinear.Rotate(-robotSpaceRotation);
    }

    Vector2 Drivetrain::CalculateAngularVelocity(const SwerveModuleMeta& meta) const {
        // desired angular velocity from the input swerve request
        float desiredAngular = m_Request.velocity.angular_velocity;

        // compute instantaneous linear velocity along edge of drivetrain as distance along an arc
        // C = theta * R
        // dC/dt = dtheta/dt * R
        // V = omega * R
        float distanceToCenter = meta.CenterOffset.Length();
        float desiredRotationalLinear = desiredAngular * distanceToCenter;

        // +y in module space is in the +theta direction (counter-clockwise).
        auto angularVector = Vector2(0.f, desiredRotationalLinear);

        // cartesian right-handed angle of center offset vector
        float centerOffsetAngle = std::atan2(meta.CenterOffset.Y, meta.CenterOffset.X);

        // however, this vector is in the rotation space of the cartesian theta angle of the
        // vector offset from the robot's center of rotation. we need to rotate it so that its
        // completely in module space
        float offsetDifference = meta.RotationalOffset - centerOffsetAngle;
        return angularVector.Rotate(-offsetDifference);
    }

    void Drivetrain::Update(const std::chrono::duration<float>& delta) {
        // update sim handlers, if there are any
        for (const auto& handler : m_SimHandlers) {
            handler->Update(delta);
        }

        // reset instantaneous odometry
        m_Odometry.velocity.x = 0.f;
        m_Odometry.velocity.y = 0.f;
        m_Odometry.velocity.angular_velocity = 0.f;

        for (size_t i = 0; i < m_Modules.size(); i++) {
            const auto& meta = m_Modules[i];

            // calculate velocity vectors
            auto moduleLinear = CalculateLinearVelocity(meta);
            auto moduleAngular = CalculateAngularVelocity(meta);

            // total desired module space velocity vector
            Vector2 moduleVelocity = moduleLinear + moduleAngular;

            // use the distance along an arc formula to convert the ground velocity of the module to
            // the angular velocity of the wheel
            float desiredAngularVelocity = moduleVelocity.Length() / m_Config.WheelRadius;

            // convert module linear velocity from x,y to theta,r
            ModuleState target;
            if (desiredAngularVelocity < std::numeric_limits<float>::epsilon()) {
                target.WheelAngularVelocity = 0.f;
                target.WheelAngle = meta.Module->GetState().WheelAngle;
            } else {
                target.WheelAngularVelocity = desiredAngularVelocity;
                target.WheelAngle = std::atan2(moduleVelocity.Y, moduleVelocity.X);
            }

            // update module with new target
            meta.Module->SetTarget(target);
            meta.Module->Update();

            // retrieve data from module state
            const auto& state = meta.Module->GetState();
            float robotSpaceWheelAngle = meta.RotationalOffset + state.WheelAngle;
            float wheelAngularVelocity = state.WheelAngularVelocity;
            float moduleVelocityLength = wheelAngularVelocity * m_Config.WheelRadius;

            Vector2 robotModuleVelocity;
            robotModuleVelocity.X = moduleVelocityLength * std::cos(robotSpaceWheelAngle);
            robotModuleVelocity.Y = moduleVelocityLength * std::sin(robotSpaceWheelAngle);
            auto absoluteModuleVelocity = robotModuleVelocity.Rotate(m_Odometry.transform.rotation);

            size_t moduleCount = m_Modules.size();
            m_Odometry.velocity.x += absoluteModuleVelocity.X / moduleCount;
            m_Odometry.velocity.y += absoluteModuleVelocity.Y / moduleCount;
            m_Odometry.velocity.angular_velocity += std::sin(state.WheelAngle) *
                                                    moduleVelocityLength *
                                                    meta.CenterOffset.Length() / moduleCount;
        }
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

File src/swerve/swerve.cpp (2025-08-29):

#include "pancakepch.h"
#include "pancake/swerve/swerve.h"

#include "pancake/config.h"

#include <librevfree/CanBus.h>

namespace pancake {
    void from_json(const nlohmann::json& src, Vector2& dst) {
        src["X"].get_to(dst.X);
        src["Y"].get_to(dst.Y);
    }

    void to_json(nlohmann::json& dst, const Vector2& src) {
        dst["X"] = src.X;
        dst["Y"] = src.Y;
    }
}; // namespace pancake

namespace pancake::swerve {
    template <typename _Ty>
    void from_json(const nlohmann::json& src, PID<_Ty>& dst) {
        src["P"].get_to(dst.Proportional);
        src["I"].get_to(dst.Integral);
        src["D"].get_to(dst.Derivative);
    }

    template <typename _Ty>
    void from_json(const nlohmann::json& src, SVA<_Ty>& dst) {
        src["S"].get_to(dst.Sign);
        src["V"].get_to(dst.Velocity);
        src["A"].get_to(dst.Acceleration);
    }

    template <typename _Ty>
    void from_json(const nlohmann::json& src, MotorConstants<_Ty>& dst) {
        src["PID"].get_to(dst.Feedback);
        src["Feedforward"].get_to(dst.Feedforward);
    }

    void from_json(const nlohmann::json& src, SwerveFunction& dst) {
        src["Constants"].get_to(dst.Constants);
        src["GearRatio"].get_to(dst.GearRatio);
        src["VoltageLimit"].get_to(dst.VoltageLimit);
        src["VoltageDeadzone"].get_to(dst.VoltageDeadzone);
    }

    void from_json(const nlohmann::json& src, SwerveModuleDesc& dst) {
        src["CenterOffset"].get_to(dst.CenterOffset);
        src["RotationalOffset"].get_to(dst.RotationalOffset);
        src["DriveID"].get_to(dst.Drive);
        src["RotationID"].get_to(dst.Rotation);
    }

    static const std::unordered_map<std::string, RotationEncoderMode> s_ModeMap = {
        { "Motor", RotationEncoderMode::Motor }, { "Output", RotationEncoderMode::Output }
    };

    void from_json(const nlohmann::json& src, RotationEncoderConfig& dst) {
        src["GearRatio"].get_to(dst.GearRatio);

        auto modeName = src["Mode"].get<std::string>();
        auto it = s_ModeMap.find(modeName);

        if (it != s_ModeMap.end()) {
            dst.Mode = it->second;
        } else {
            throw std::runtime_error("Invalid encoder mode!");
        }
    }

    void from_json(const nlohmann::json& src, SwerveFeatures& dst) {
        src["UseCosineCompensation"].get_to(dst.UseCosineCompensation);
    }

    void from_json(const nlohmann::json& src, Drivetrain::Config& dst) {
        src["Network"].get_to(dst.Network);
        src["WheelRadius"].get_to(dst.WheelRadius);
        src["Drive"].get_to(dst.Drive);
        src["Rotation"].get_to(dst.Rotation);
        src["Modules"].get_to(dst.Modules);
        src["RotationEncoder"].get_to(dst.EncoderConfig);
        src["Features"].get_to(dst.Features);
    }

    template <typename _Ty>
    void to_json(nlohmann::json& dst, const PID<_Ty>& src) {
        dst["P"] = src.Proportional;
        dst["I"] = src.Integral;
        dst["D"] = src.Derivative;
    }

    template <typename _Ty>
    void to_json(nlohmann::json& dst, const SVA<_Ty>& src) {
        dst["S"] = src.Sign;
        dst["V"] = src.Velocity;
        dst["A"] = src.Acceleration;
    }

    template <typename _Ty>
    void to_json(nlohmann::json& dst, const MotorConstants<_Ty>& src) {
        dst["PID"] = src.Feedback;
        dst["Feedforward"] = src.Feedforward;
    }

    void to_json(nlohmann::json& dst, const SwerveFunction& src) {
        dst["Constants"] = src.Constants;
        dst["GearRatio"] = src.GearRatio;
        dst["VoltageLimit"] = src.VoltageLimit;
        dst["VoltageDeadzone"] = src.VoltageDeadzone;
    }

    void to_json(nlohmann::json& dst, const SwerveModuleDesc& src) {
        dst["CenterOffset"] = src.CenterOffset;
        dst["RotationalOffset"] = src.RotationalOffset;
        dst["DriveID"] = src.Drive;
        dst["RotationID"] = src.Rotation;
    }

    void to_json(nlohmann::json& dst, const RotationEncoderConfig& src) {
        dst["GearRatio"] = src.GearRatio;

        bool modeFound = false;
        for (const auto& [name, mode] : s_ModeMap) {
            if (mode == src.Mode) {
                dst["Mode"] = name;

                modeFound = true;
                break;
            }
        }

        if (!modeFound) {
            throw std::runtime_error("Invalid encoder mode!");
        }
    }

    void to_json(nlohmann::json& dst, const SwerveFeatures& src) {
        dst["UseCosineCompensation"] = src.UseCosineCompensation;
    }

    void to_json(nlohmann::json& dst, const Drivetrain::Config& src) {
        dst["Network"] = src.Network;
        dst["WheelRadius"] = src.WheelRadius;
        dst["Drive"] = src.Drive;
        dst["Rotation"] = src.Rotation;
        dst["Modules"] = src.Modules;
        dst["RotationEncoder"] = src.EncoderConfig;
        dst["Features"] = src.Features;
    }

    Swerve::Swerve(bool sim) : Node("swerve") {
        Drivetrain::Config config;
        config.Drive = config.Rotation = {};

        // measurements taken from CAD
        // https://cad.onshape.com/documents/a3570f35688a1cf16e8e4419/v/433e7b2f8e33ea9906b8780e/e/a1fbf0c2138da401bd4bce14
        config.Network = "can0";
        config.WheelRadius = 1.5f * 0.0254f; // in meters
        config.Drive.GearRatio = 2.f / 5.f;
        config.Rotation.GearRatio = 1.f / 48.f;
        config.Drive.VoltageLimit = config.Rotation.VoltageLimit = 12.f;
        config.Drive.VoltageDeadzone = config.Rotation.VoltageDeadzone = 0.02f;
        config.EncoderConfig.Mode = RotationEncoderMode::Output;
        config.EncoderConfig.GearRatio = -1.f;
        config.Features.UseCosineCompensation = true;

        auto bus = rev::CanBus::Get(config.Network);
        sim |= !bus->IsOpen();

        if (!LoadConfig(get_name(), config)) {
            if (sim) {
                for (size_t i = 0; i < 4; i++) {
                    float angle = std::numbers::pi_v<float> * (1.f / 4.f + i / 2.f);

                    SwerveModuleDesc simModule;
                    simModule.CenterOffset = { std::cos(angle), std::sin(angle) };
                    simModule.RotationalOffset = angle;
                    simModule.Drive = 2 + i * 2;
                    simModule.Rotation = 1 + i * 2;

                    config.Modules.push_back(simModule);
                }
            }

            SaveConfig(get_name(), config);
        }

        m_Drivetrain = std::make_shared<Drivetrain>(config, sim);

        const auto& modules = m_Drivetrain->GetModules();
        for (size_t i = 0; i < modules.size(); i++) {
            auto modulePath = "/pancake/swerve/module/mod" + std::to_string(i);
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

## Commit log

2024-08-21 add controller list
    [robot.xml]
2024-08-21 swerve node
    [robot.xml]
2024-08-22 switch to chassis speeds
2024-08-22 add main robot node
    [robot.xml]
2024-08-26 fix pid controller and start tests
    [swerve.cpp]
2024-08-26 update revlib and add encoder calls
2024-08-26 add odometry and refactor messages
2024-08-27 fix unit tests and math
    [drivetrain.cpp]
2024-08-30 set temp pid
2024-09-14 add support for absolute encoder
2024-10-12 use all encoders
2024-10-23 fix speed on drive motor to account for wheel well rotation
    [swerve_module.cpp]
2024-10-24 fix signs and optimize build
    [swerve.cpp, swerve_module.cpp]
2024-10-31 client imgui and pid/sva service
2024-11-05 start drivetrain view
2024-11-05 drivetrain listeners
2024-11-05 drivetrain view complete
2024-11-06 fix wheel straightening
2024-11-06 fix jitter?
2024-11-06 pass through devices in docker compose
2024-11-07 switch to self-hosted runner
2024-11-11 initial urdf
    [2020_-_m3_t-nut_v2.stl, 6812zz_ball.stl, 6812zz_inner_ring.stl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]
2024-11-12 config for my tool
    [2020_-_m3_t-nut_v2.stl, 6812zz_ball.stl, 6812zz_inner_ring.stl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]
2025-05-05 fix config in non-docker sim
    [swerve.cpp]
2025-06-06 voltage limits
2025-06-12 dynamic pid tuning
2025-06-20 voltage deadzone
2025-06-26 switch to debian in build stage
2025-06-26 fix build errors :3c
    [drivetrain.cpp, swerve_module.cpp]
2025-07-29 temp disable angle correction
    [swerve_module.cpp]
2025-07-29 undo correction removal and fix angular velocity
    [drivetrain.cpp, swerve_module.cpp]
2025-08-05 reset defaults to avoid angle issues
    [swerve.cpp]
2025-08-07 verify potential angle reset
    [drivetrain.cpp]
